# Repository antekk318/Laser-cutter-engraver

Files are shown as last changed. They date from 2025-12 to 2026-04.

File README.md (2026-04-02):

# Las-XY - a laser engraver ⚙️

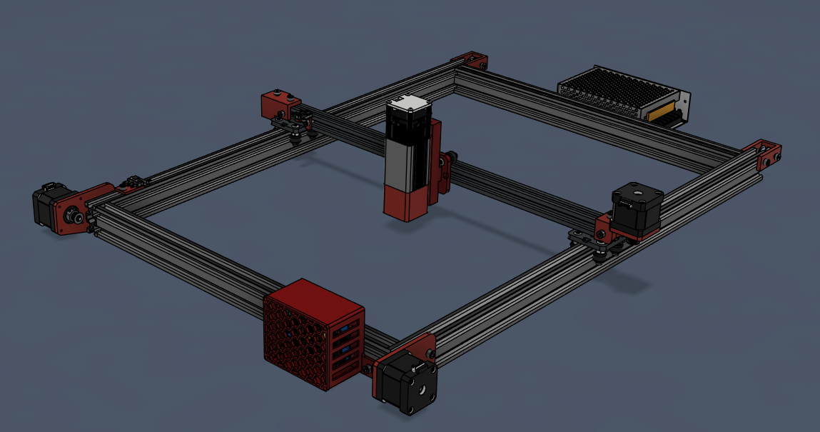
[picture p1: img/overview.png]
3D model

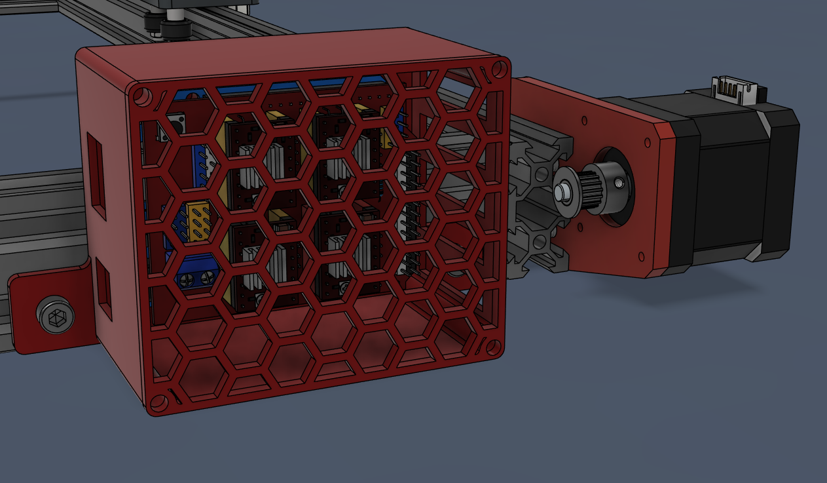
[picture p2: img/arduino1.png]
3dmodel


This is a laser cutter project designed by myself. The idea came from the need of such tool and not wanting to spend a load of money on prebuilt ones. Besides, it has been a great learning opportunity for me as I've never made such thing before and this was my first encounter with CAD.

## Overview

**1. Tools**
* 3D printer,
* Hex screwdrivers,
* soldering iron

**2. Parts**
* Laser module,
* 2020 and 2040 aluminium extrusions, roller gantrys
* 3x Nema 17 stepper motor,
* Arduino Uno + CNC Shield + 3 stepper drivers,

*Screws and nuts:*
```
The project uses metric, rounded head hex screws, ranging from M3 to M5.

To mount parts to the aluminium profile, it uses t-slot nuts, and for the rest - standard hexagon nuts.

! Additionally, one >50mm long M5 bolt is needed for the sliding mechanism of the laser mount !
```
**For the exact parts I've used, please refer to the BOM.**

**3. Software**

GRBL, Universal G-Code Sender, Arduino IDE, Fusion 360

## [Wiring manual](wiring-manual.md)

## Setup

Once the machine is assembled and wired, firmware needs to be installed so that it can move.
Flashing GRBL onto the Arduino.
GRBL is the firmware which is going to run on the Arduino and interpret the G-code commands. The installation is fairly simple.

1. Download the Arduino IDE from their site, a program which allows to flash the Arduino with firmware.
2. Download GRBL source code.zip file from the GitHub repository: https://github.com/gnea/grbl/releases and unzip the grbl file. Before we proceed a we need to modify the config.h file inside grbl to account for the lack of the Z axis.

configh1

change that to:

configh2

Next, it is crucial to put jumpers on the pins marked red, to clone the A axis with X.

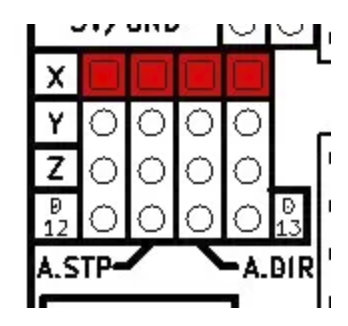
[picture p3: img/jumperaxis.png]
A axis jumpers


Open Arduino IDE and import the grbl file via: Sketch->Include Library->add .zip library (it says .zip but the uncompressed file should be chosen).
Navigate to the grblUpload sketch via: File -> Examples -> grbl -> grblUpload
Connect the Arduino to the PC via USB (make sure the correct board and port is selected).
Flash the sketch through Sketch->Upload
Connecting the Arduino to LaserGRBL(through which I will control the laser) is fairly simple. First, download LaserGRBL from their website: https://lasergrbl.com and install it. Second, connect the Arduino to the computer via USB, choose the correct port and select "115200" band rate, then click connect. If the console shows "Grbl 1.1h, the chip is connected.

Now the important part. The laser needs to be correctly configured so that it won't damage itself. Fortunately, there is an instruction concerning the vital settings there: https://lasergrbl.com/wp-content/uploads/2020/05/Grbl-Configuration-ENG.pdf on the LaserGRBL website. Some of them are the length, direction and speed of the axis, homing direction, laser power and the calibration of the stepper motors.

## BOM

|Product name |Product description |Price ($)|Amount |Total price ($)|Link |
|---|---|---|---|---|---|
|Laser tree LT-20W |Laser module, 4W optical power |34,09 |1 |34,09 |https://pl.aliexpress.com/item/1005003306807390.html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,scm-url:1007.40050.354490.0,pvid:efae0e2c-adf3-4440-94dc-df6932cc5b3b,tpp_buckets:668%232846%238107%231934&pdp_ext_f=%7B%22order%22%3A%22545%22%2C%22spu_best_type%22%3A%22price%22%2C%22eval%22%3A%221%22%2C%22sceneId%22%3A%2230050%22%2C%22fromPage%22%3A%22recommend%22%7D&pdp_npi=6%40dis%21USD%2137.88%2134.09%21%21%2137.88%2134.09%21%40211b80e117668627392187425e7a82%2112000035196145458%21rec%21PL%212719169016%21XZ%211%210%21n_tag%3A-29919%3Bd%3A5a5a8e15%3Bm03_new_user%3A-29895%3BpisId%3A5000000197181459&utparam-url=scene%3ApcDetailTopMoreOtherSeller%7Cquery_from%3A%7Cx_object_id%3A1005003306807390%7C_p_origin_prod%3A|
|Nema 17 |Stepper motor |8,54 |3 |25,62 |https://pl.aliexpress.com/item/1005008459399126.html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 |
|PSU 12V 10A |Power supply |12,32 |1 |12,32 |https://pl.aliexpress.com/item/33051556213.html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 |
|Full Controller |Arduinio Uno + CNC shield + stepper drivers |11,27 |1 |11,27 |https://pl.aliexpress.com/item/1005009968121020.html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 |
|2020 Extrusion 550mm |- |9,49 |1 |9,49 |https://pl.aliexpress.com/item/1005004679698586.html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 |
|2040 Extrusion 700mm |- |19,11 |2 |38,22 |https://pl.aliexpress.com/item/1005004679698586.html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 |
|2040 Extrusion 450mm |- |13,24 |2 |26,48 |https://pl.aliexpress.com/item/1005004679698586.html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 |
|Wheels for 2020 rollers|3pcs |5,29 |1 |5,29 |https://pl.aliexpress.com/item/1005007494205467.html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 |
|2020 V-slot Gantry |2pcs |11,49 |1 |11,49 |https://pl.aliexpress.com/item/1005007487312327.html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 |
|16T Sprocket |5mm bore, 6mm belt width |1,94 |3 |5,82 |https://pl.aliexpress.com/item/1005004863292486.html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 |
|16T idler wheel |5mm bore, 6mm belt width |2,1 |3 |6,3 |https://pl.aliexpress.com/item/1005006739452921.html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 |
|Limit switch with wheel|5pcs |1,44 |1 |1,44 |https://pl.aliexpress.com/item/1005008233825861.html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 |
|Gt2 6mm belt |4 meters |9,35 |1 |9,35 |https://pl.aliexpress.com/item/1005004822740666.html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 |
|Male jumper wires |For the limit switches |- | | | |
|Normal wire |For the PSU |- | | | |
|C14 Connector |Perosonal choice for connecting the PSU to the mains|- | | | |
|Screws and nuts |I already have them |- |Total cost ($):|197,18 | |

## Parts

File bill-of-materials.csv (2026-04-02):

Product name | Product description | Price ($) | Amount | Total price ($) | Link
Laser tree LT-20W | Laser module, 4W optical power | 34,09 | 1 | 34,09 | https://pl.aliexpress.com/item/1005003306807390.html?scm_id=1007.40050.354490.0&scm-url=1007.40050.354490.0
Nema 17 | Stepper motor | 8,54 | 3 | 25,62 | https://pl.aliexpress.com/item/1005008459399126.html?sourceType=1
PSU 12V 10A | Power supply | 12,32 | 1 | 12,32 | https://pl.aliexpress.com/item/33051556213.html?sourceType=1
Full Controller | Arduinio Uno + CNC shield + stepper drivers | 11,27 | 1 | 11,27 | https://pl.aliexpress.com/item/1005009968121020.html?curPageLogUid=XIXIk9VCUSM3
2020 Extrusion 550mm | - | 9,49 | 1 | 9,49 | https://pl.aliexpress.com/item/1005004679698586.html
2040 Extrusion 700mm | - | 19,11 | 2 | 38,22 | https://pl.aliexpress.com/item/1005004679698586.html?curPageLogUid=1pm48O7g5ZjH
2040 Extrusion 450mm | - | 13,24 | 2 | 26,48 | https://pl.aliexpress.com/item/1005004679698586.html?curPageLogUid=1pm48O7g5ZjH
Wheels for 2020 rollers | 3pcs | 5,29 | 1 | 5,29 | https://pl.aliexpress.com/item/1005007494205467.html
2020 V-slot Gantry | 2pcs | 11,49 | 1 | 11,49 | https://pl.aliexpress.com/item/1005007487312327.html?sourceType=1
16T Sprocket | 5mm bore, 6mm belt width | 1,94 | 3 | 5,82 | https://pl.aliexpress.com/item/1005004863292486.html
16T idler wheel | 5mm bore, 6mm belt width | 2,1 | 3 | 6,3 | https://pl.aliexpress.com/item/1005006739452921.html
Limit switch with wheel | 5pcs | 1,44 | 1 | 1,44 | https://pl.aliexpress.com/item/1005008233825861.html
Gt2 6mm belt | 4 meters | 9,35 | 1 | 9,35 | https://pl.aliexpress.com/item/1005004822740666.html?curPageLogUid=HJARXSEXvHsa
Male jumper wires | For the limit switches | -
Normal wire | For the PSU | -
C14 Connector | Perosonal choice for connecting the PSU to the mains | -
Screws and nuts | I already have them | - | Total cost ($): | 197,18

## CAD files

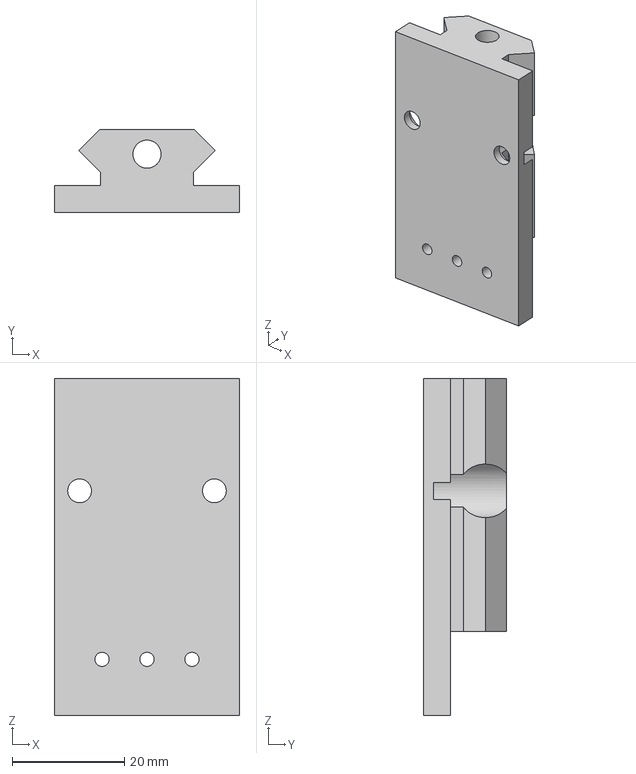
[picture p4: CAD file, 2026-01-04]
CAD/sliding mount LT-40WAA.step
33.0 x 14.8 x 60.0 mm

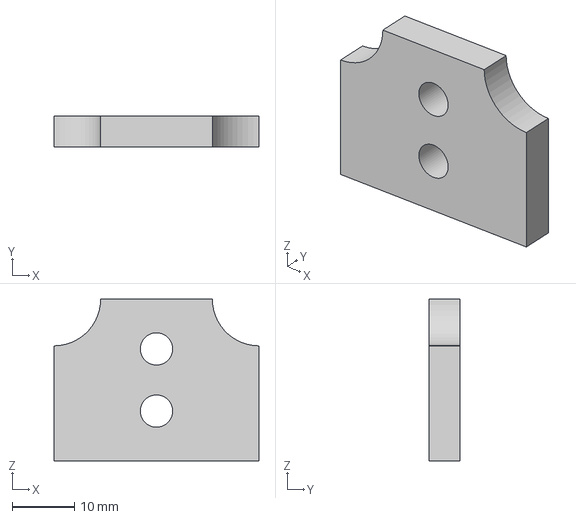
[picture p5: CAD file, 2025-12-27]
CAD/static mount 2.step
33.0 x 5.00 x 26.0 mm

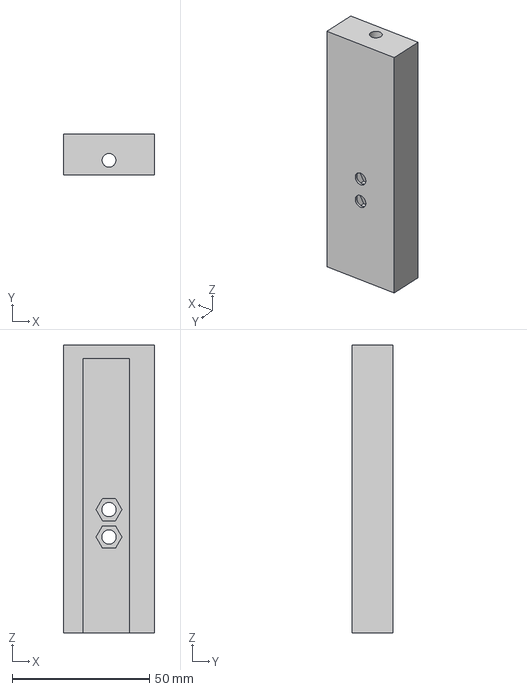
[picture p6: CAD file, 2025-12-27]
CAD/static mount 1.step
33.0 x 15.0 x 105.0 mm

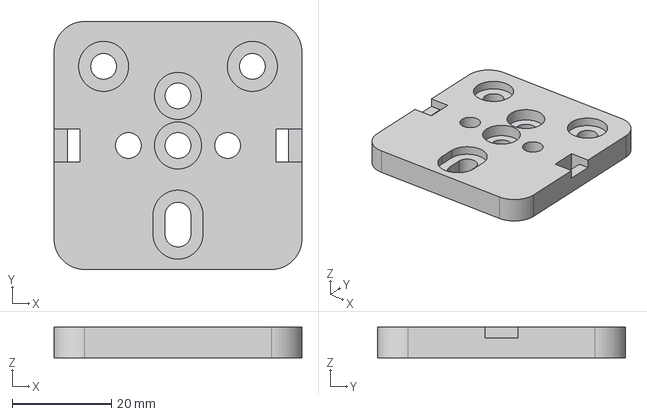
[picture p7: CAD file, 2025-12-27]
CAD/3 wheel gantry base.step
50.0 x 50.0 x 6.25 mm

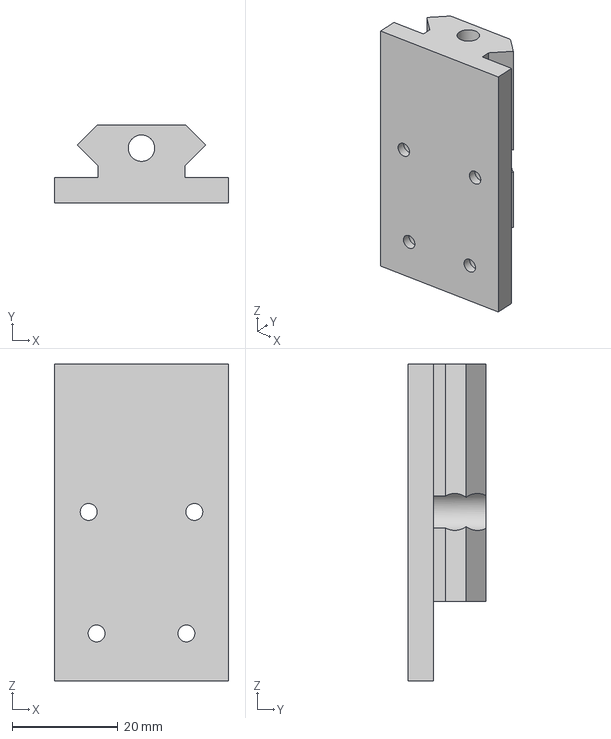
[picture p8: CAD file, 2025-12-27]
CAD/sliding mount LT20W.step
33.0 x 14.8 x 60.0 mm

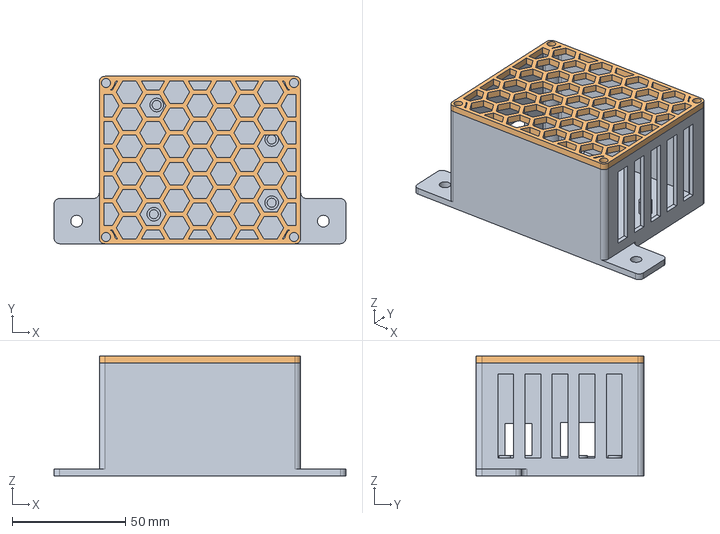
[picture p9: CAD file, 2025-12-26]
CAD/arduino box.step
129.0 x 74.0 x 53.0 mm

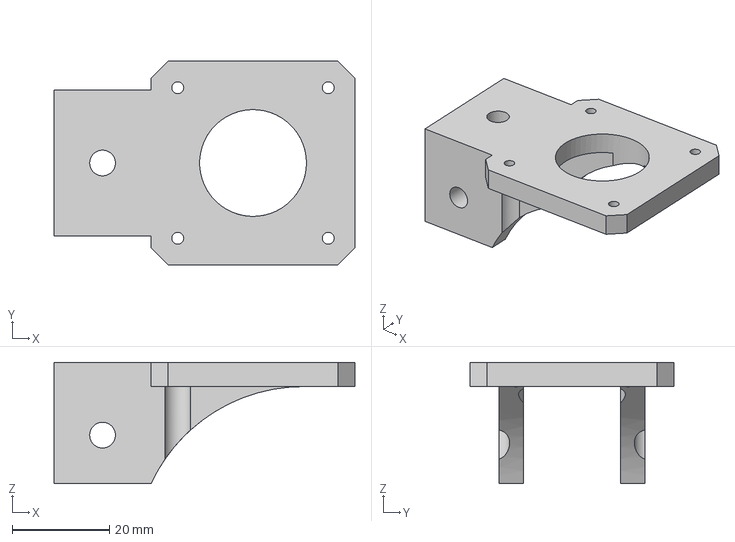
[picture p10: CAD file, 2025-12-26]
CAD/X motor mount.step
62.0 x 42.0 x 25.0 mm

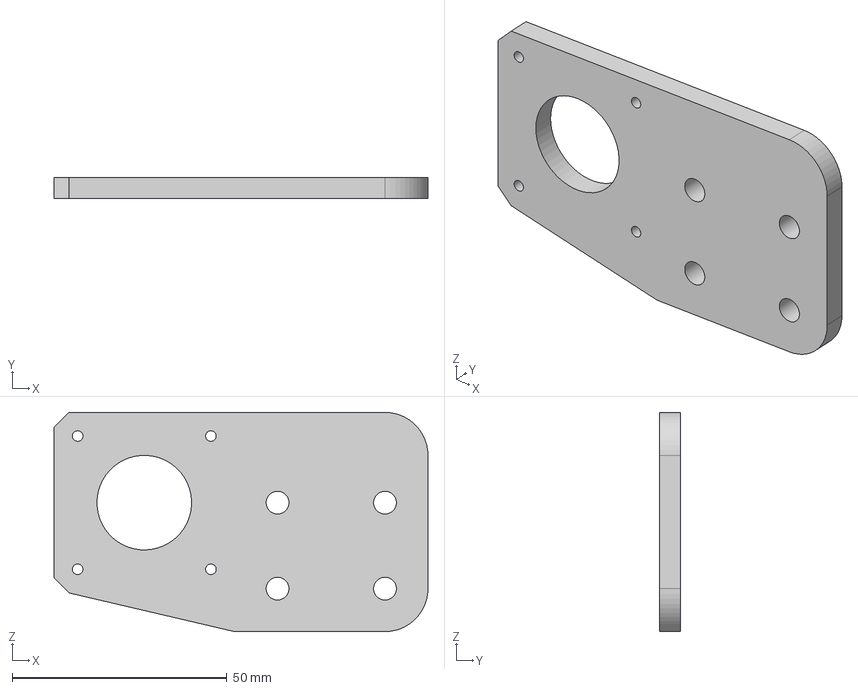
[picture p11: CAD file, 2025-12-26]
CAD/Y motor mount.step
87.0 x 5.00 x 51.0 mm

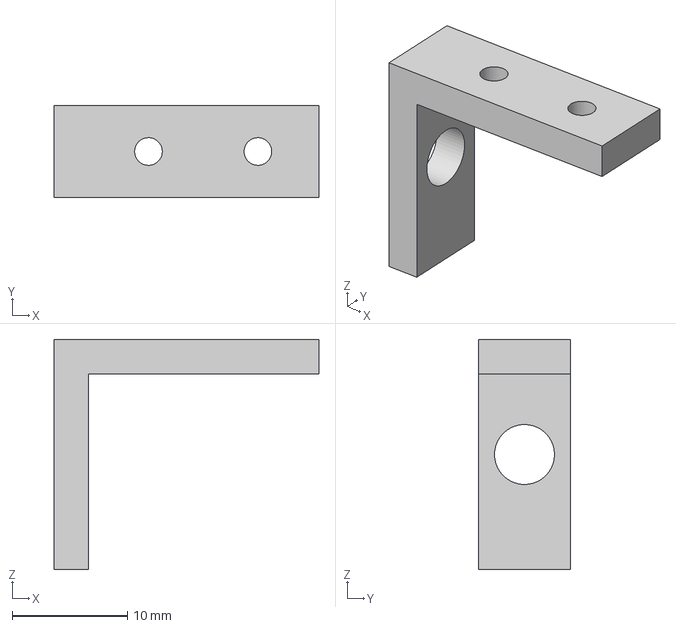
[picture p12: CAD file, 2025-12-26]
CAD/limit switch bracket X.step
23.0 x 8.00 x 20.0 mm

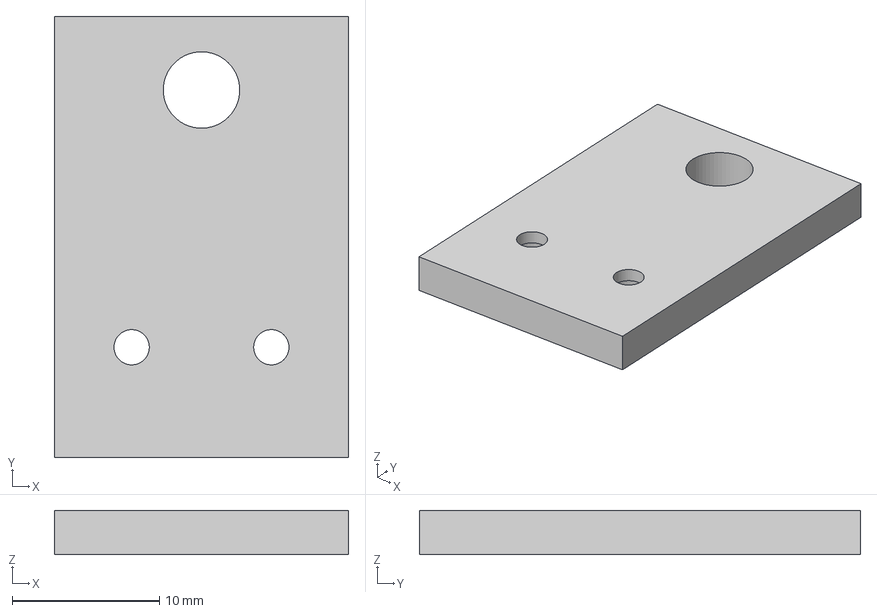
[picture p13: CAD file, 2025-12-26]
CAD/limit switch Y mount.step
20.0 x 30.0 x 3.00 mm

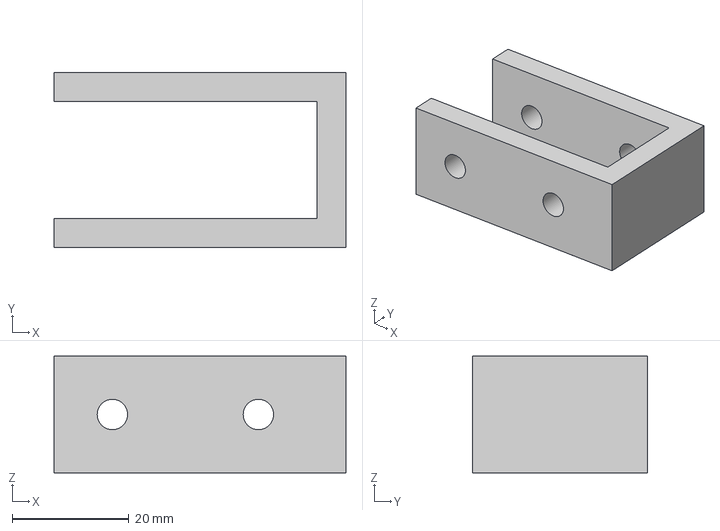
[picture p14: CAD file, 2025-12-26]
CAD/Y sprocket bracket.step
50.0 x 30.0 x 20.0 mm

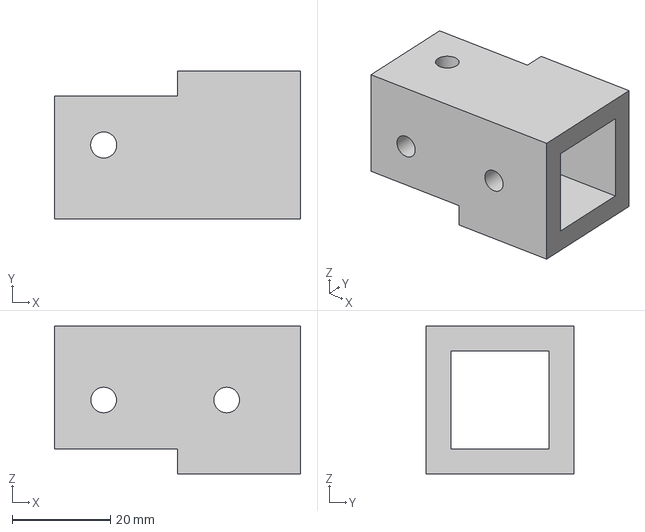
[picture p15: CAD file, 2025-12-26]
CAD/X sprocket bracket.step
50.0 x 30.0 x 30.0 mm

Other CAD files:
CAD/Laser engraver.f3d

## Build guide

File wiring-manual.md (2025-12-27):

## This is how to wire the machine to the CNC shield.

1. Attach the CNC shield on top of the arduino.
2. Enable the board by placing a jumper on those two pins.

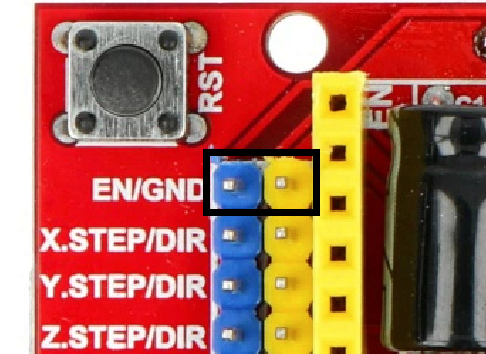
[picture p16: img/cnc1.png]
cnc shield 1
   

4. Place jumpers on the micro step resolution for each driver, I'm using a DRV8825 driver and I'll select M1. I consulted the table I found inside this document on page 8: https://bulkman3d.com/wp-content/uploads/2019/04/CNC-Shield-Guide-BM-v1.0.pdf
 
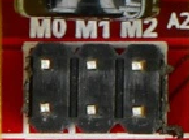
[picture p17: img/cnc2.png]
cnc shield 2
  

5. Place the stepper drivers in their designated places.

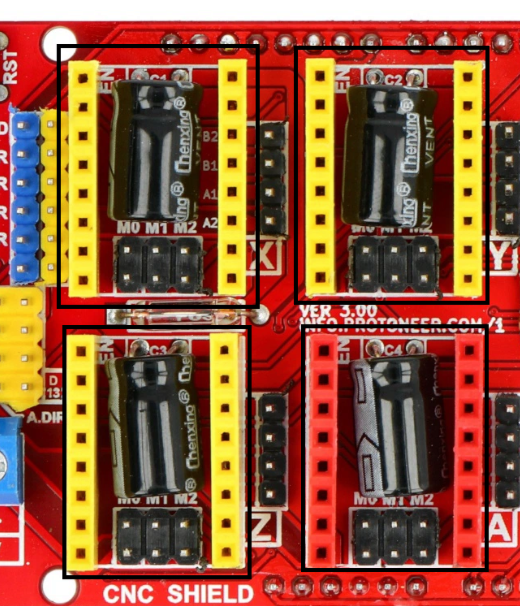
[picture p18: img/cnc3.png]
cnc shield 3
   

6. Connect the stepper motors to the pins next to the drivers, the orientation isn't important since it can be configured in the software if the motor is spinning the wrong way.

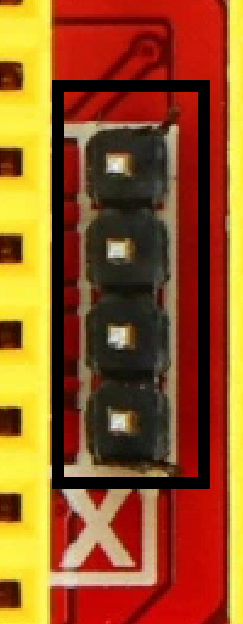
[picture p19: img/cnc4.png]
cnc shield 4
   

7. Connect the limit switches.

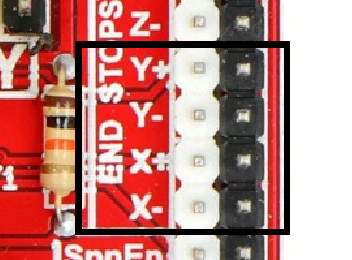
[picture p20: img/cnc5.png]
cnc shield 5
   

8. Connect the laser. The laser should have the pins labeled on the PCB. The 12V + and - wires should go to the PSU or the 12V screws terminal on the CNC shield. The third wire which carries the PWM signal goes to the Z+ or Z- limit switch pin.

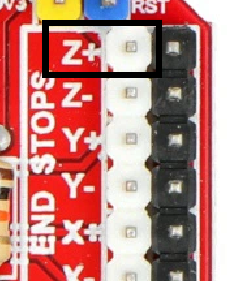
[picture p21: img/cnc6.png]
cnc shield 6
   

9. Connect the PSU.

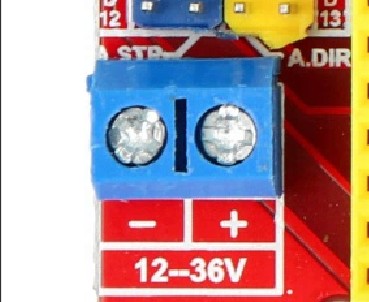
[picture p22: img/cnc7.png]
cnc psu
    

The best way I've seen to keep the laser wires sturdy and outside the workspace, yet still able to move freely, is to zip tie them to a piece of filament.

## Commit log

2025-12-26 Create CAD
2025-12-27 Update and rename Arkusz kalkulacyjny bez tytułu - Arkusz1.csv to bill-of-materials.csv
    [bill-of-materials.csv]
2026-01-04 Update and rename sliding mount.step to sliding mount LT20W.step
    [sliding mount LT20W.step]
2026-04-02 Rename Arkusz kalkulacyjny bez tytułu - Arkusz1.csv to bill-of-materials.csv
    [bill-of-materials.csv]
